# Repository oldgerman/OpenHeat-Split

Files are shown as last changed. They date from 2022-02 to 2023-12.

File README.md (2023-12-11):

# OpenHeat-Split

> 使用[朱雀固件](https://gitee.com/createskyblue/OpenT12)，PCB从[OpenHeat](https://github.com/peng-zhihui/OpenHeat)修改，主控引脚都不变，oled和编码器做成小板
>
> 该项目还包括热床外壳安装等~~一条龙服务~~
>
> <span style="color:rgb(255, 50, 50);">免责声明：不恰当的安装可能危及您的生命安全，请确保有一定的强电安全知识！</span>
>
> 本资料为压缩包版，不保证为最新版，最新版请访问[Github仓库](https://github.com/oldgerman/OpenHeat-Split)

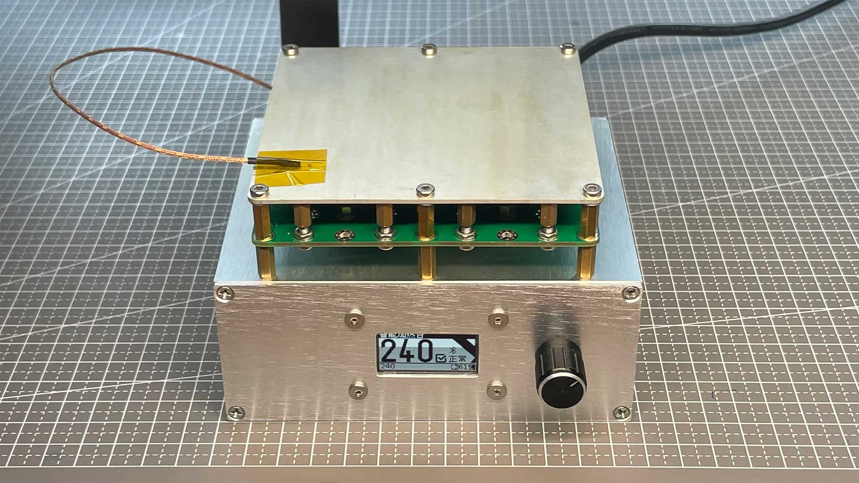
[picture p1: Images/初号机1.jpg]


## 控制板

- 使用0603封装、可靠性高的连接器
- oled和编码器做成单独的小板子，oled目前是1.3寸，可换2.42寸的（暂未画板，有能力的话可以自己做）
- 控制热床加热的MOS：使用便宜又大碗的TO-247封装的管子
- 推荐工作电压12~24V，电流小于18A

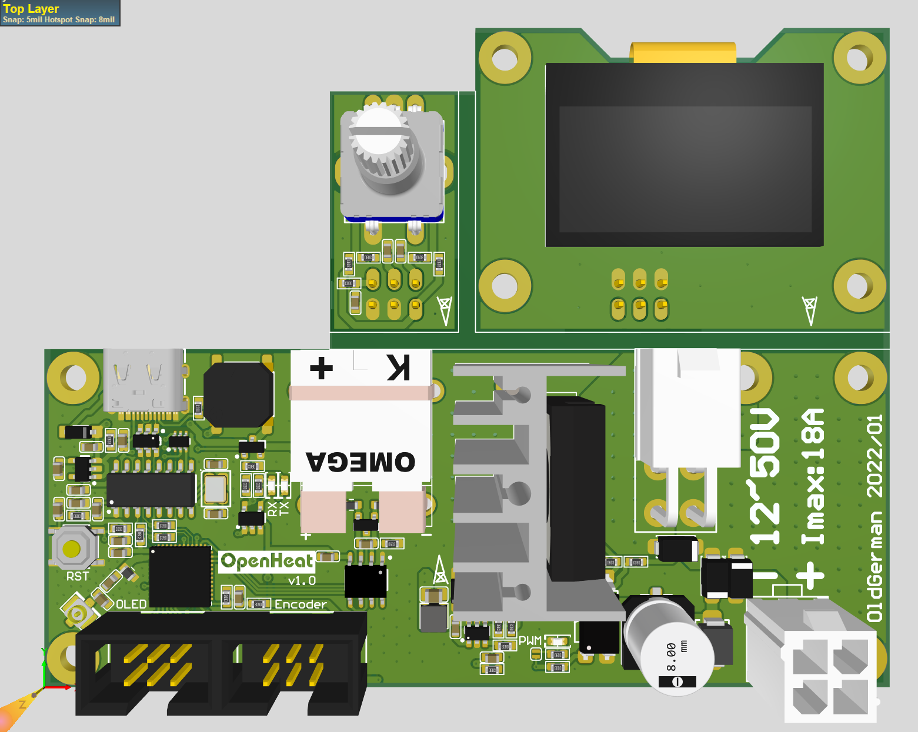
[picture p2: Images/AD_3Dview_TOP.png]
AD_3Dview
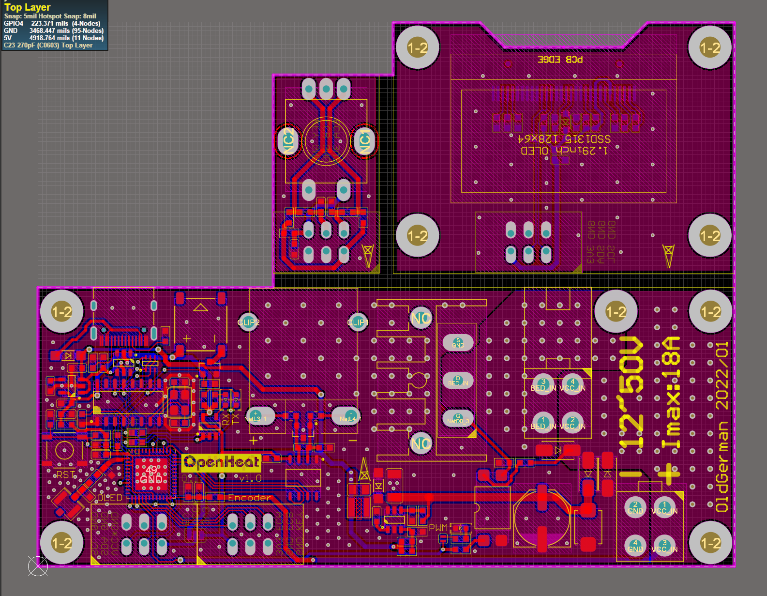
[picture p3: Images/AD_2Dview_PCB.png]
AD_2Dview
|  |  |
| --- | --- |

注：PCB为双面板，板厚1.6mm，需要分板，用壁纸刀沿着白线多划几下掰断，或者锯子伺候

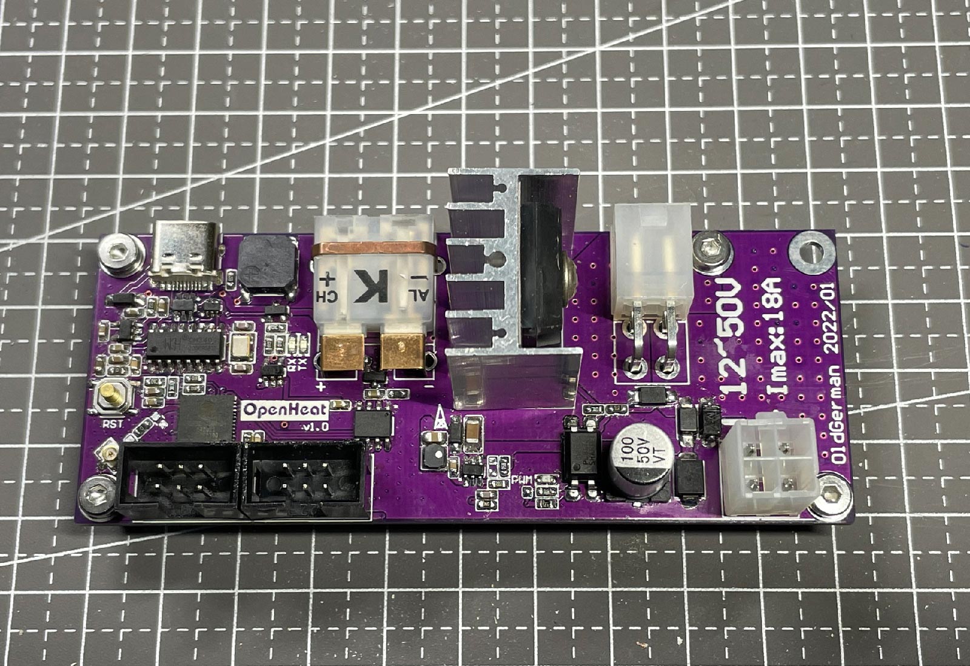
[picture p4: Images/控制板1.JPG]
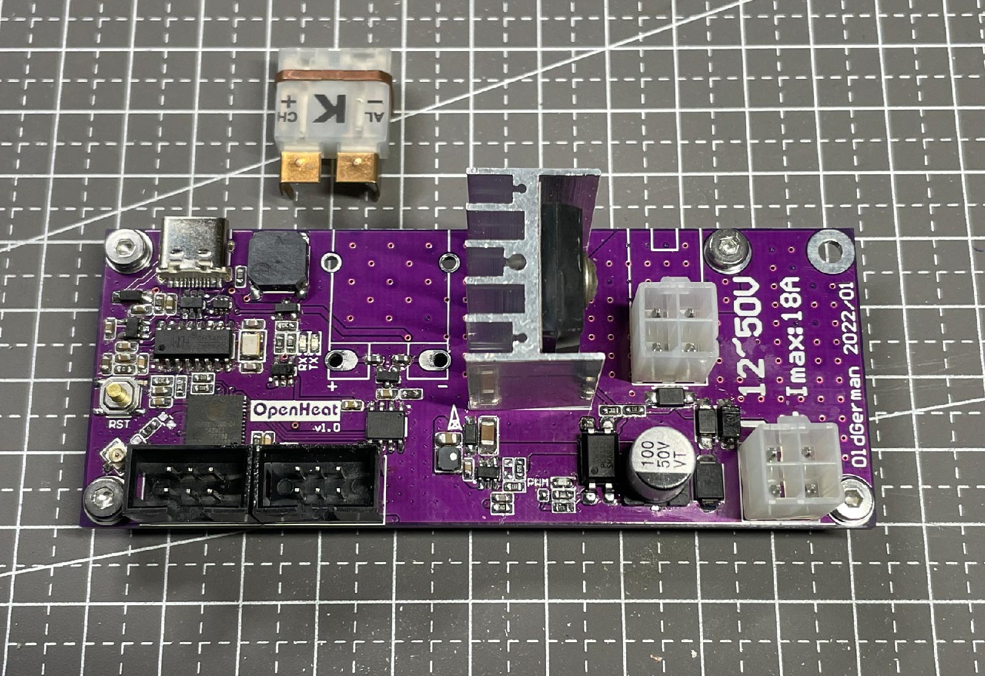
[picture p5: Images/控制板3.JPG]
|  |  |
| --- | --- |
| 接热床的4针端子使用90度的5569连接器 | 接热床的4针端子也可用垂直的5566连接器<br />若不安装K型热电偶连接器，可将热电偶丝直接焊接在焊盘上 |

## 热床

[GeekStart展硕](https://oshwhub.com/GeekStartzhan-shuo/GSH_Bed-lv-ji-ban-jia-re-ping-tai)设计的GSH Bed 12V150W版本，线宽28.347mil，实测12V只能加热到185度且此温度下功率约85W

我修改了该设计，将线加宽到43mil，两侧铜带开窗，使用类似探针方式的接触（免焊接），可通过配置“顶针”位置来兼容12V或24V，热床维持200度时功率约100W，维持230度功率约140W

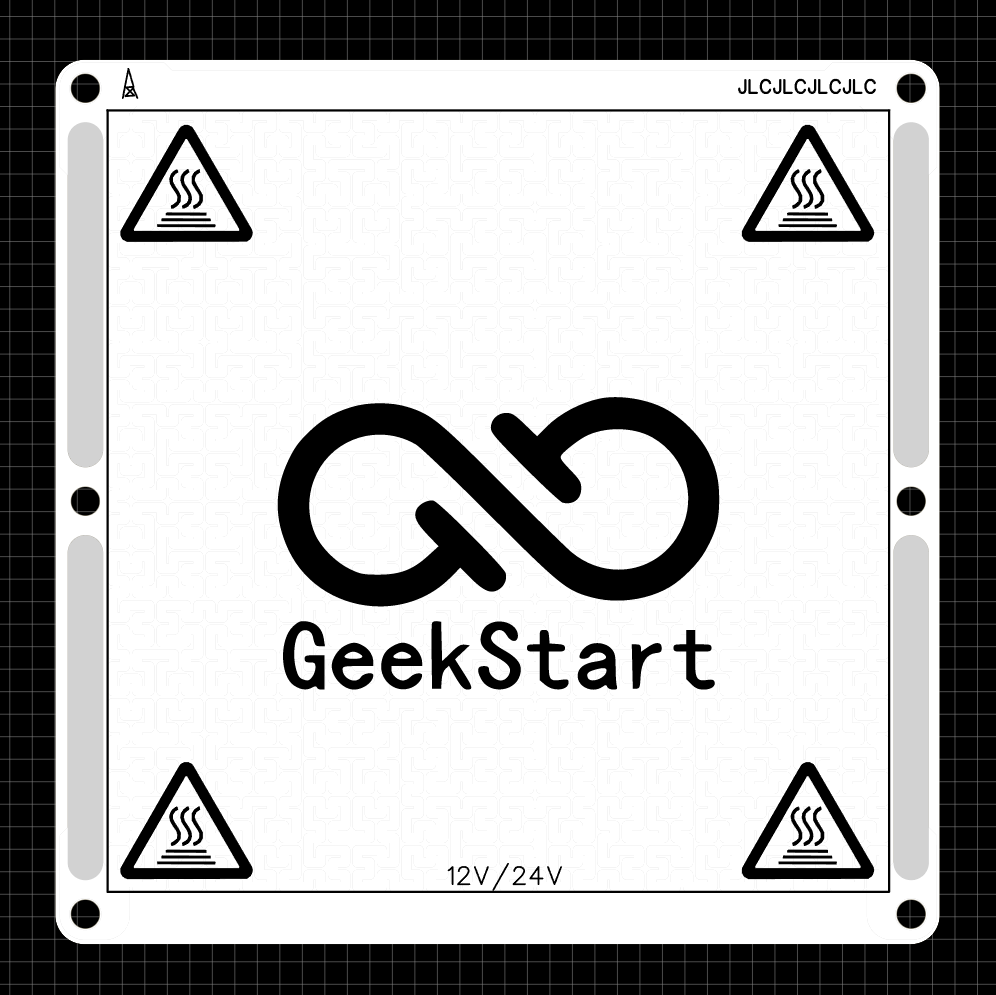
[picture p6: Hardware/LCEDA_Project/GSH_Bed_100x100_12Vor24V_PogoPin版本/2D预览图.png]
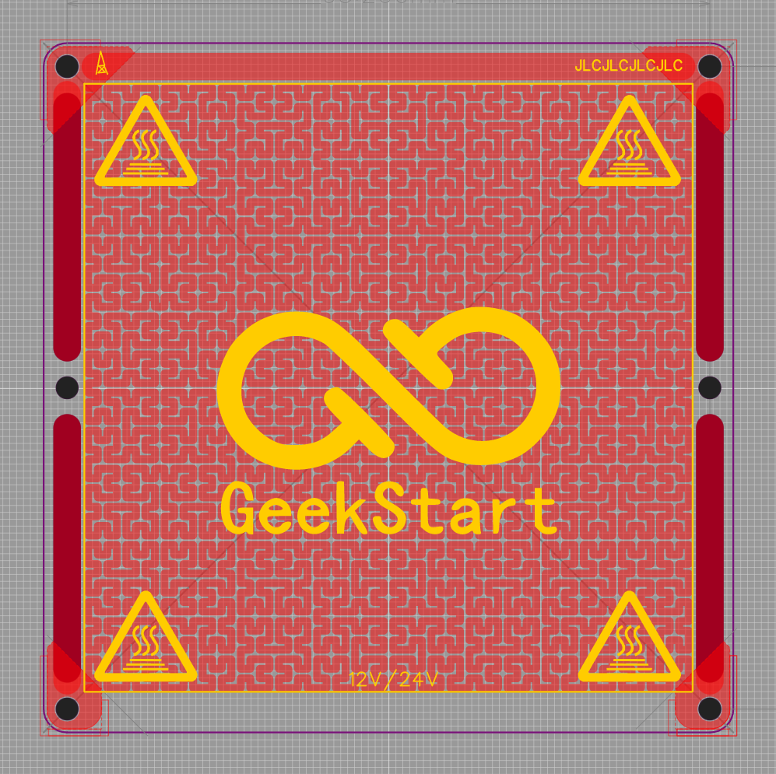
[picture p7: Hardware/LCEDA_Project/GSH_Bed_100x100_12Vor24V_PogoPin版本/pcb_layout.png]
|  |  |
| --- | --- |

### 升温测试

| 修改前：线宽28mil、Vin= 12.7V、T<sub>环境</sub> = 10℃，2段PID | 修改后：线宽43mil、Vin= 12.7V、T<sub>环境</sub> = 10℃，3段PID |
| --- | --- |
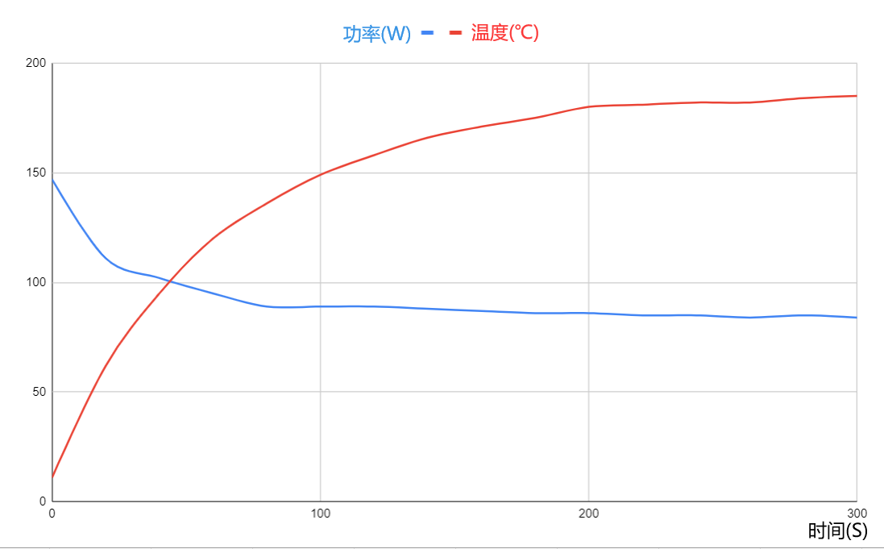
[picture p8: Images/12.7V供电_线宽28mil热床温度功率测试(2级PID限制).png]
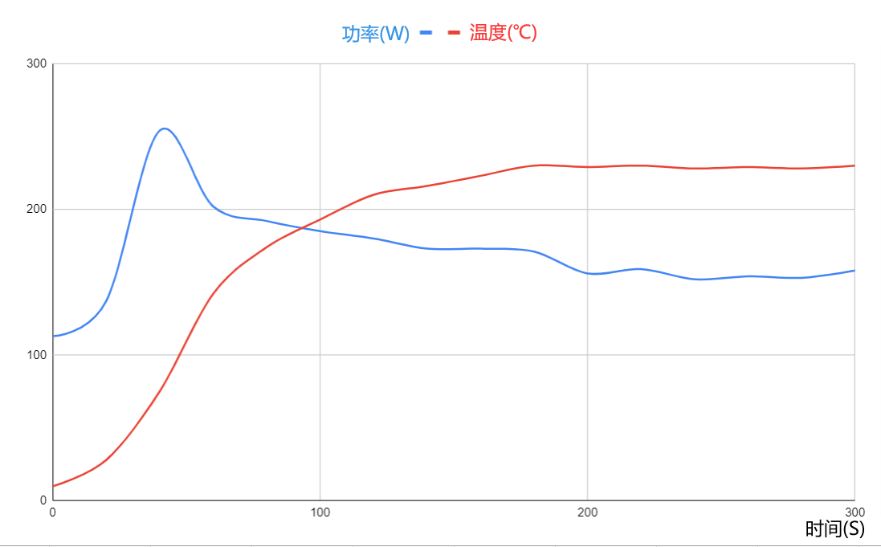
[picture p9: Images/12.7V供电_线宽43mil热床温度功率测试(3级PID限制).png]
|  |  |

## 顶针PCB

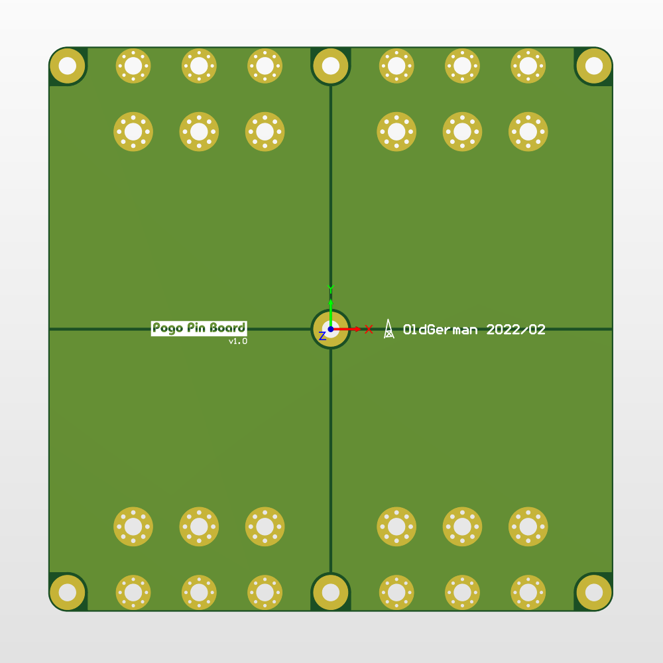
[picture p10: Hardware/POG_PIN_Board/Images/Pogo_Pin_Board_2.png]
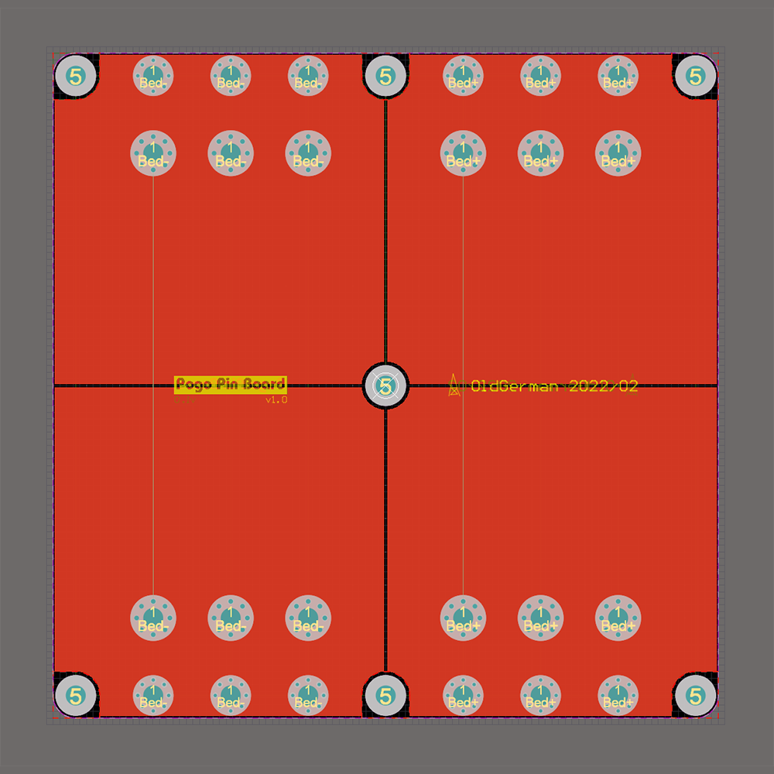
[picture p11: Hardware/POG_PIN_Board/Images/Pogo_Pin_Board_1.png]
|  |  |
| --- | --- |

### 为什么需要这块板？

1. 在铝基板和壳体之间隔热
2. 铝基板导热太强，供电线十分难焊接，且200度左右焊锡会软化
2. 我使用过[华容5A电流探针](https://item.taobao.com/item.htm?id=555813649830)与热床接触，探针铜镀金的，导热很快，当热床200度以上时探针内部的弹簧会失去弹性，使探针报废

### 顶针的位置

所以使用探针的计划翻车了，改用纯螺柱代替探针的接触方式，手搓铜柱顶住热床就行，这种接触方式姑且叫顶针吧，顶针用的螺丝螺柱的具体规格请见后文的 安装图：上壳体

可以通过配置顶针位置，使铝基板热床工作在12V或24V（许多3D打印机热床也有类似的设计），12V使用8枚顶针，24V使用4枚顶针

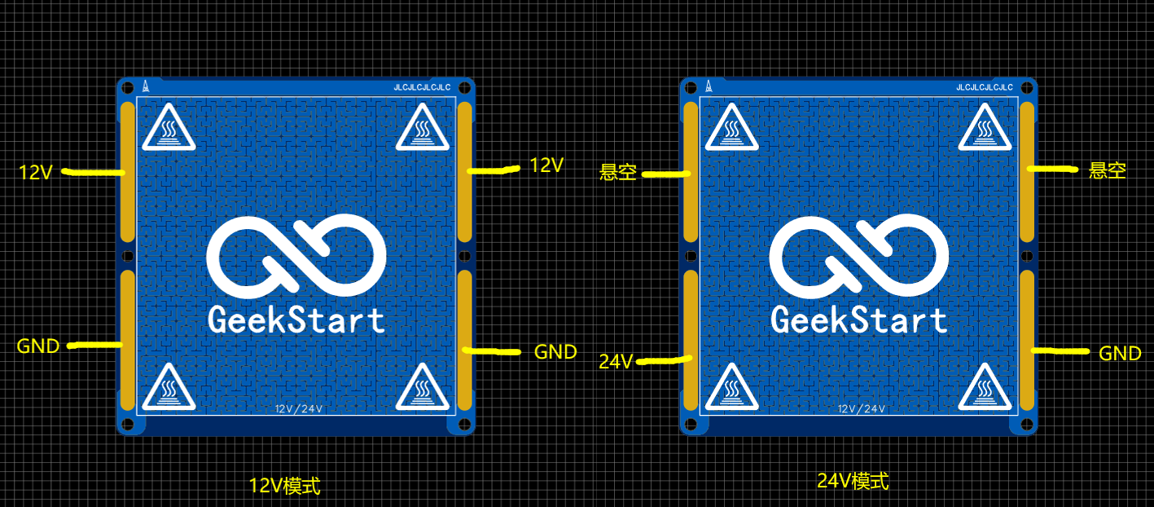
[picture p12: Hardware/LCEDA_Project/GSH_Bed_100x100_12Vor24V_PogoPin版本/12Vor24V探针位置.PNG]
12Vor24V探针位置


## 外壳

裸板并不意味着经久耐用，寻找合适的外壳是件头疼的事情

使用铝型材外壳，规格125×51×100mm，价格差不多15包邮，需要按开孔图开孔

### PCB尺寸

| | 尺寸（mm) | M3孔距（mm) |
| --- | --- | --- |
| 主控板 | 100×40 | 93.2×33.2 |
| 1.3寸OLED板 | 49×36 | 43×27 |
| 铝基板热床  | 100×100 | 93.2×93.2 |

为了做到安装不冲突，你可能需要修改本项目PCB源文件：最可能改动的是OLED小板的连接器位置，可见它并不居中，因为我根据目前用的<span style="color:rgb(0, 125, 255);">CLP0212</span>电源的尺寸做了修改，以防安装冲突

### 开关电源

电源可选型号如下，这类电源的尺寸大约是100×50mm，可以非常紧凑地安装在铝壳内

| | 开关电源 | 被动/主动散热功率(W) | 尺寸（mm) | 孔距（mm) | 加格(￥)@包邮 | 适配铝壳尺寸（mm) |
| --- | --- | --- | --- | --- | --- | --- |
| 厚度偏薄，利于前面板的模块安装 | 金升阳 LOF225 20bXX | 140/225 | 101.6×50.8×25.4  | 95.25×44.45 | 155 | 125×51×100 |
| 厚度偏厚，非常不利于前面板的模块安装 | 明纬 EPP-200-XX | 140/200 | 101.6×50.8×32 | 95.25×44.45 | 214 | 125×51×100 |
| 过气方案 | GE [CLP0212](https://library.industrialsolutions.abb.com/publibrary/checkout/CLP0212?TNR=Data%20Sheets%7CCLP0212%7CPDF) 12V | 100/200 | 101.6×50.8×37.14 | 93.2×42.4 | 45~196 | 125×51×100 |
| 又不是不能用 | [WX-DC2416](https://m.tb.cn/h.fQLvrV4?sm=300ae6) | 150/220 | 115×65×3.5 | 105.8×55.7  | 35 | 125×51×110 |

[参考：200W超小ITX电源 明纬EPP200-12性能测试](https://www.bilibili.com/read/cv14154464)

### 安装

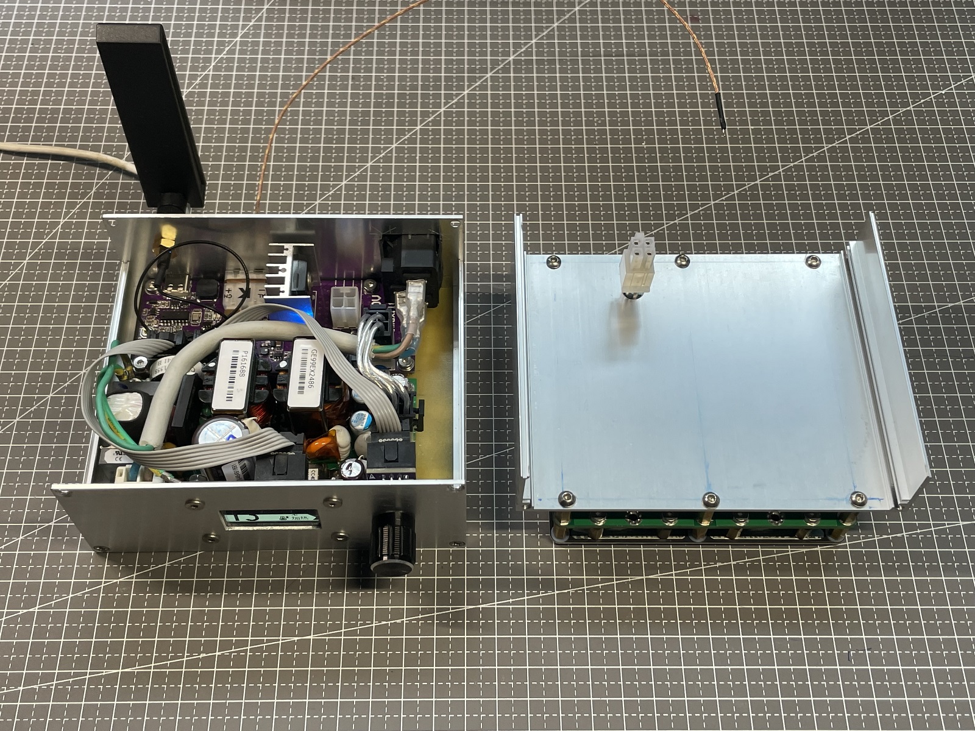
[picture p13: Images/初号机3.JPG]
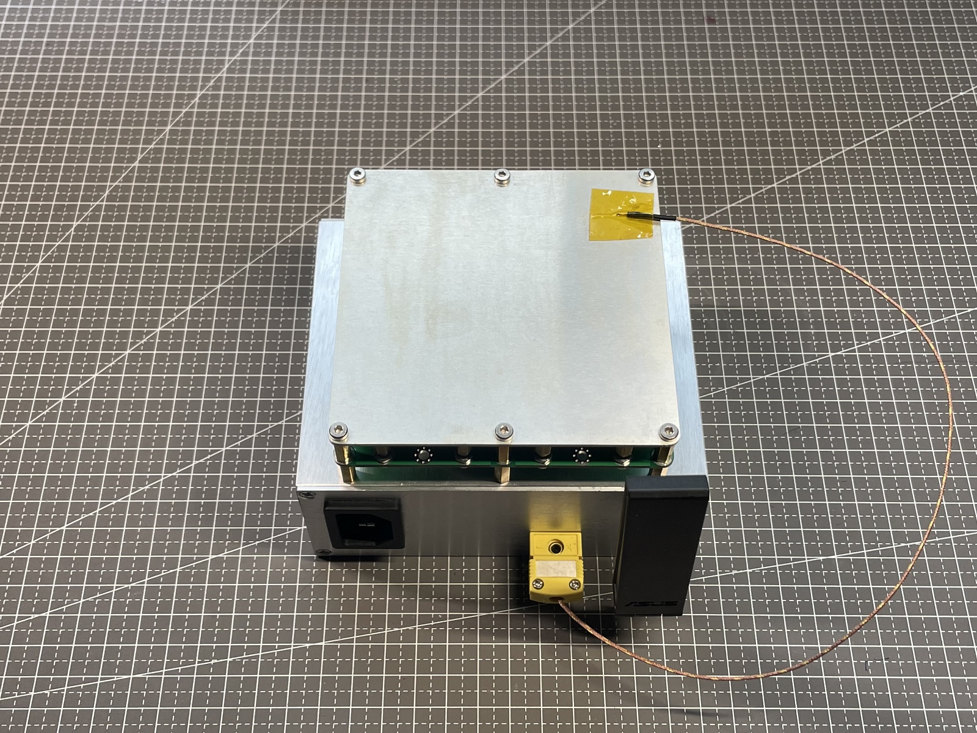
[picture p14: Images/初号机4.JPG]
| |  |  |
| --- | --- | --- |
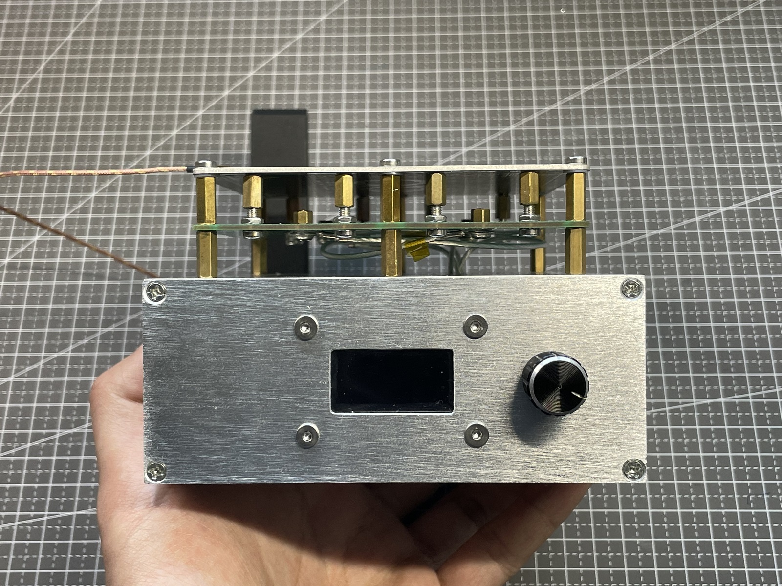
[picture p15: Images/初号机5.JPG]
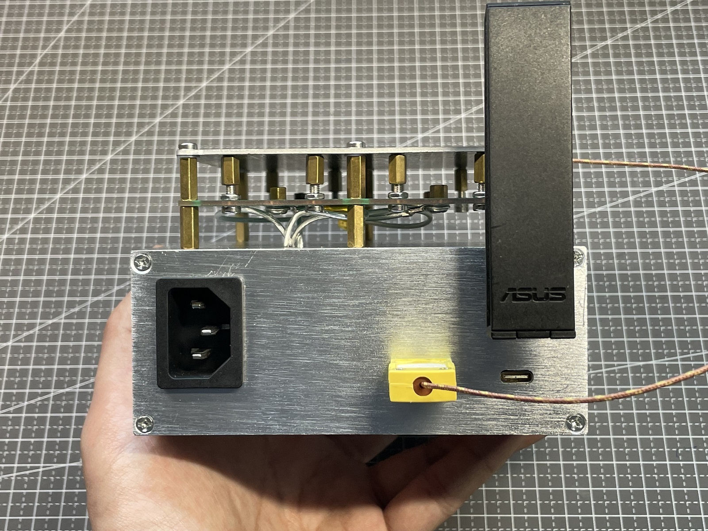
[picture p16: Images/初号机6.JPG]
| |  |  |
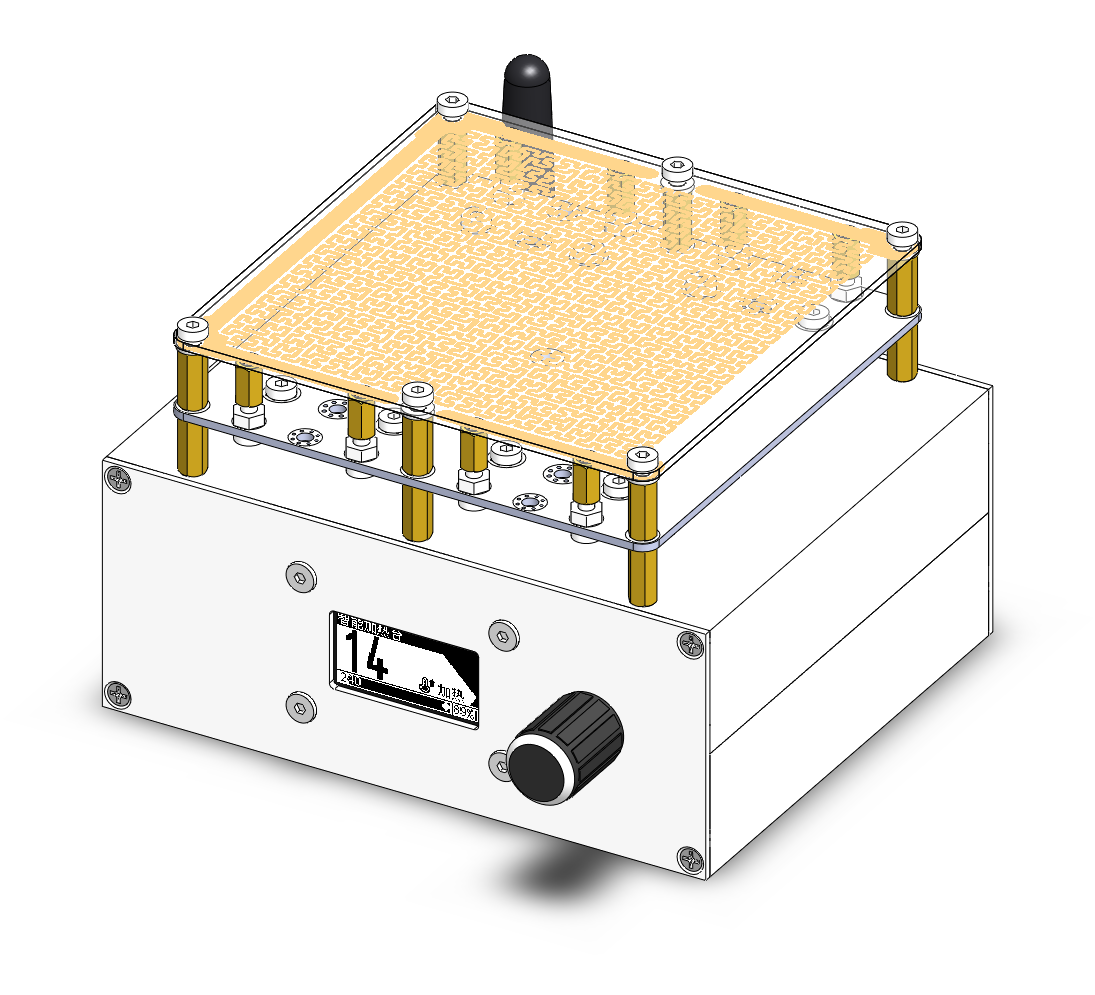
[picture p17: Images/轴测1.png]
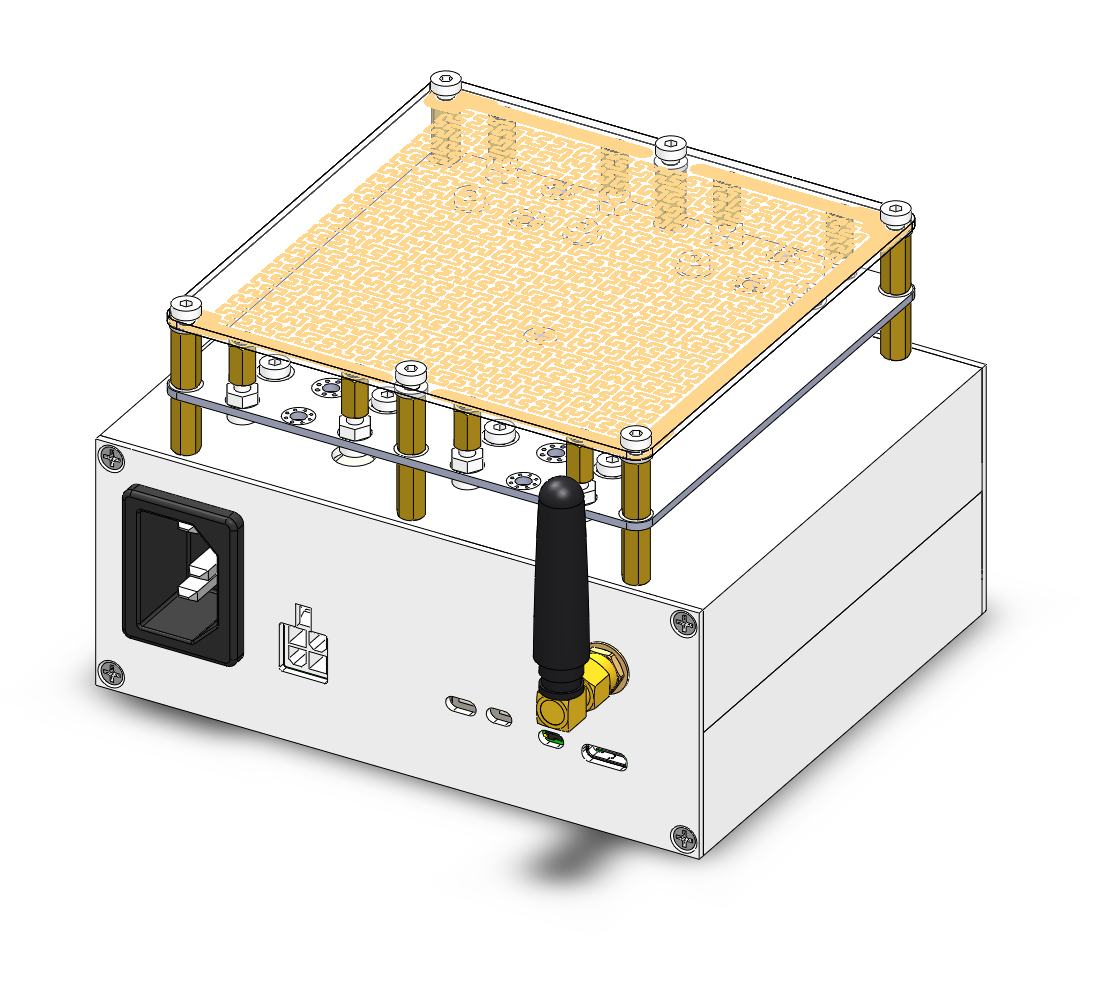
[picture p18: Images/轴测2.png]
| |  |  |
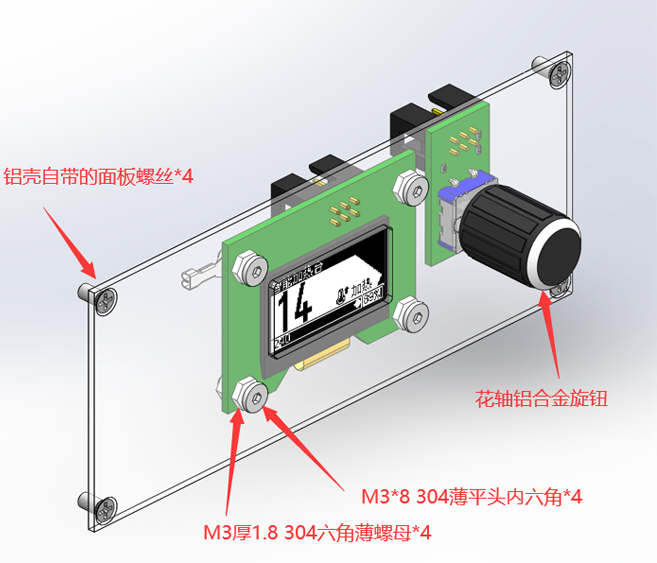
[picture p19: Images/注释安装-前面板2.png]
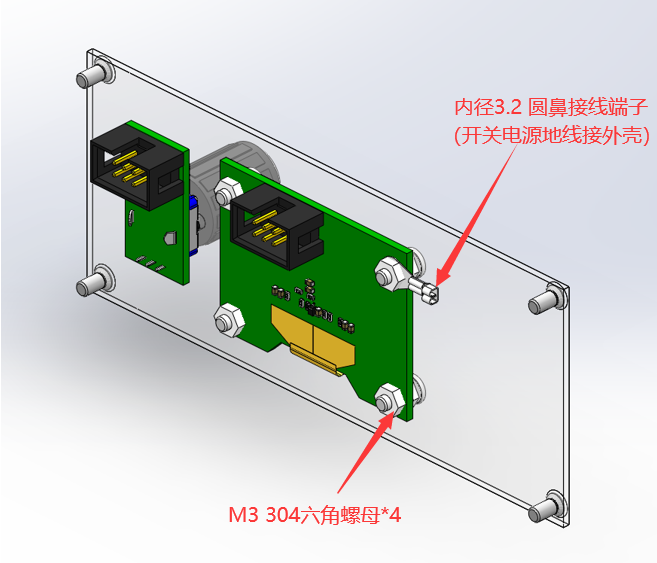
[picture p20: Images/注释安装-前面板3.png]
| 前面板 |  |  |
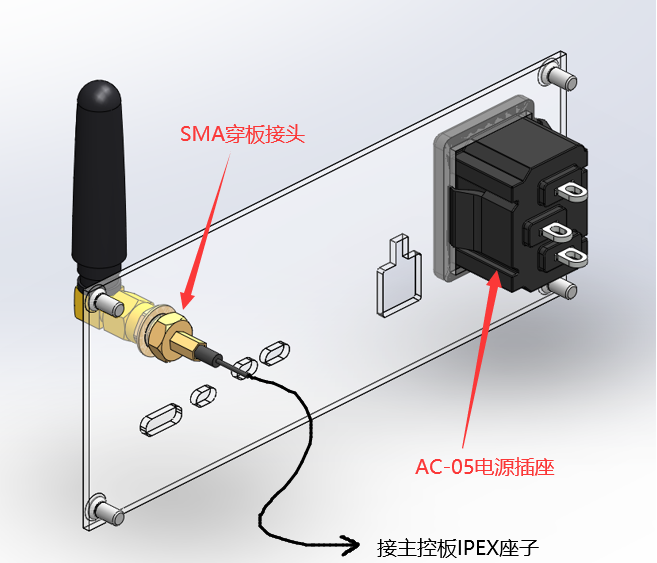
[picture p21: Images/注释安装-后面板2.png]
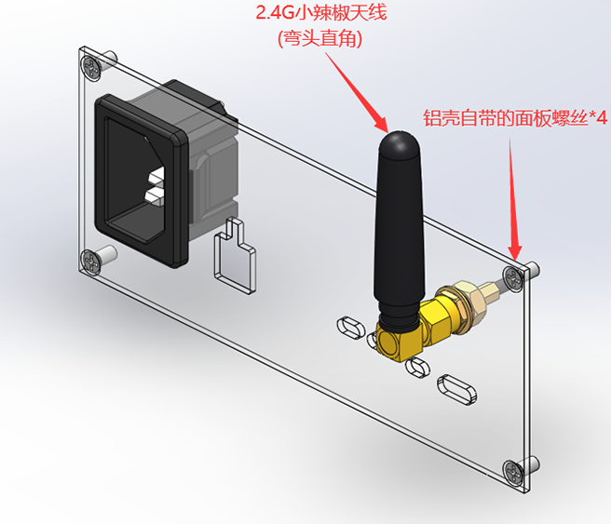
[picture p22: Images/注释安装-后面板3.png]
| 后面板 |  |  |
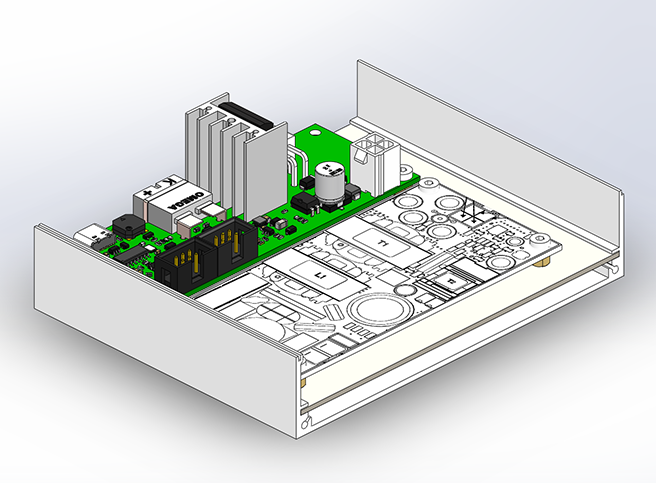
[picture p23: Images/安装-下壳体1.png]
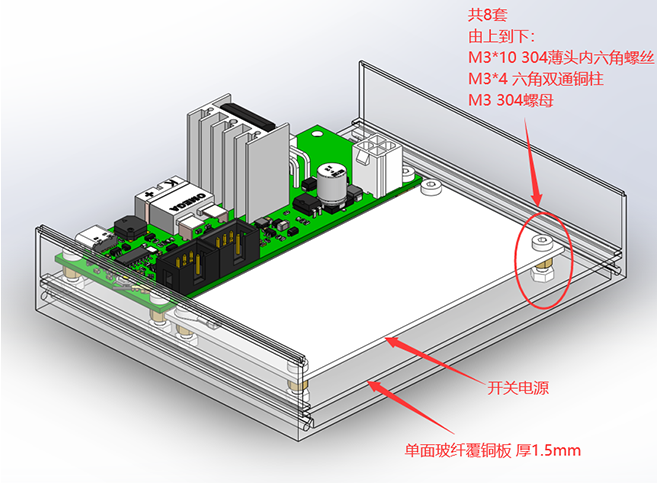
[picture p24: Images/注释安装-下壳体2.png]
| 下壳体 |  |  |
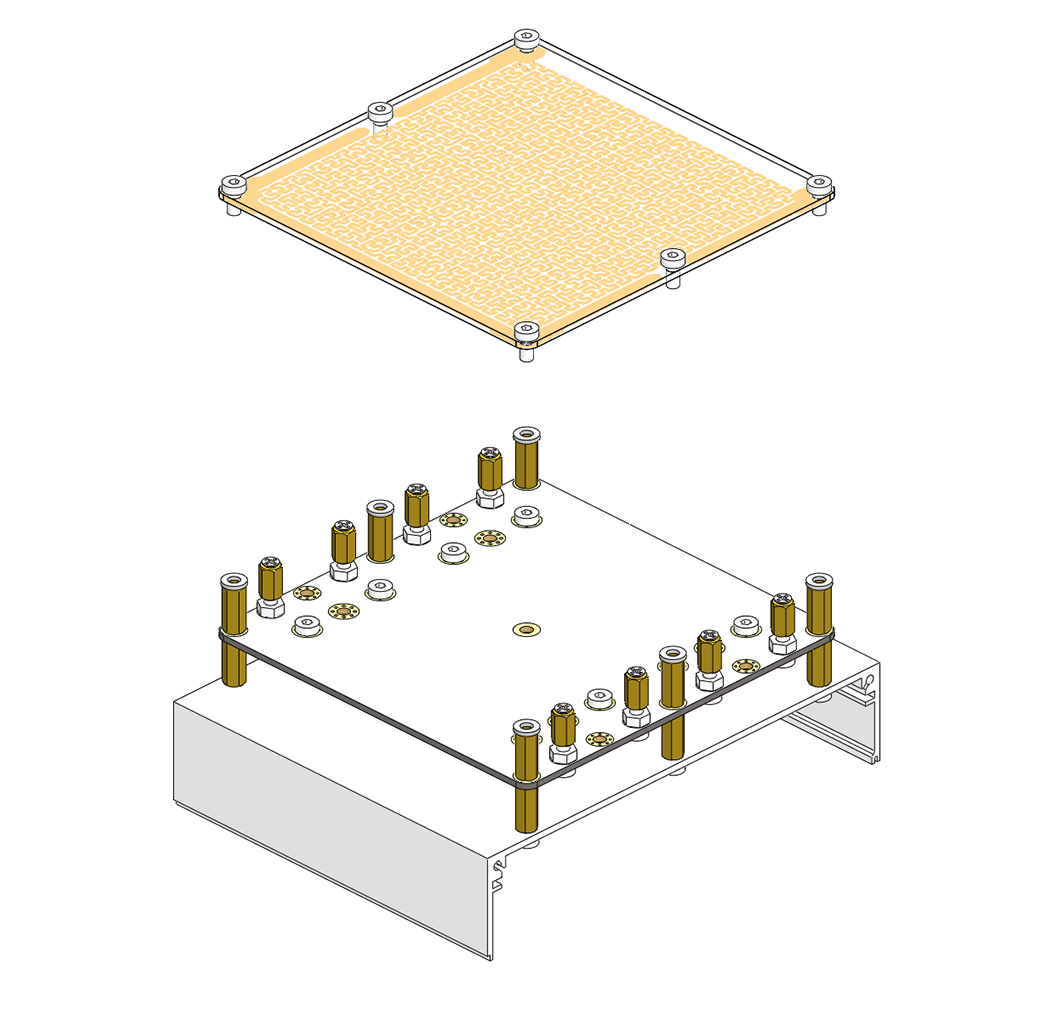
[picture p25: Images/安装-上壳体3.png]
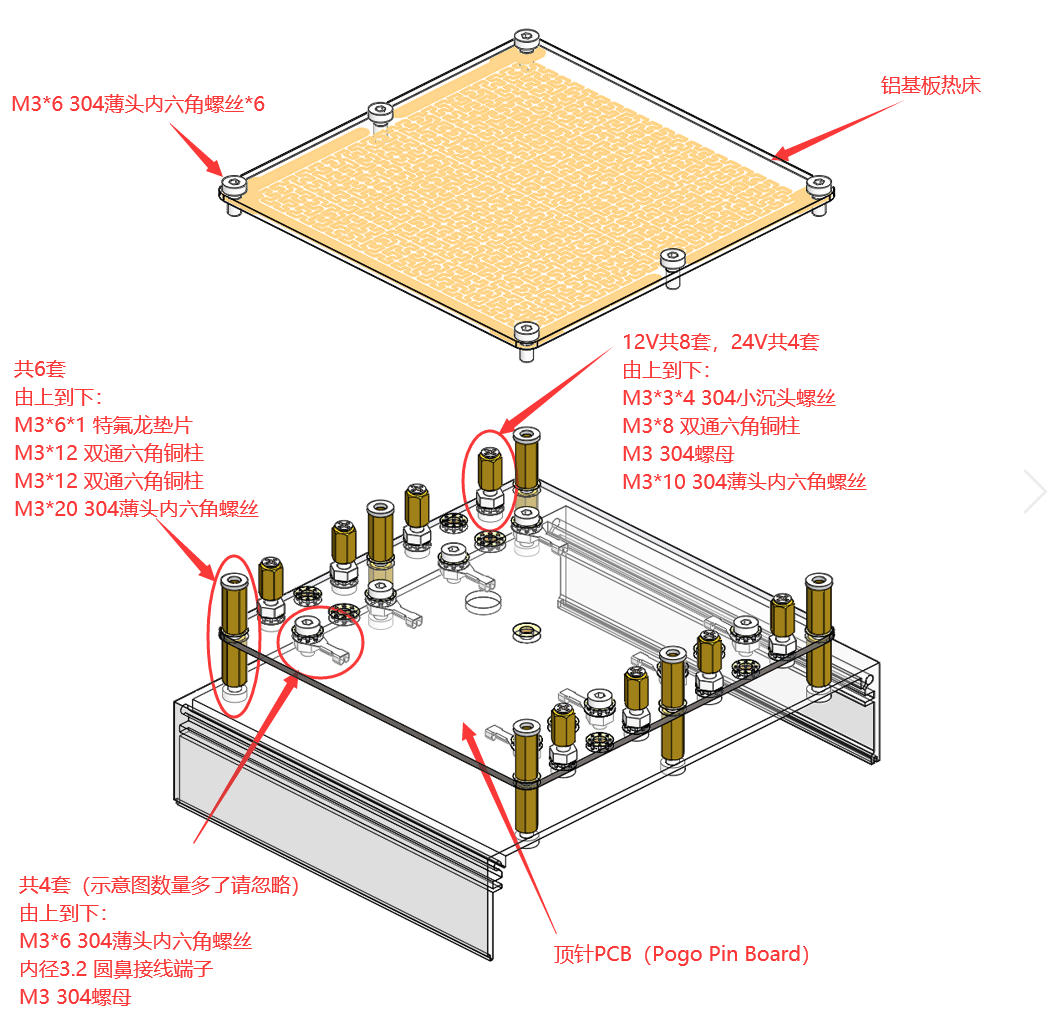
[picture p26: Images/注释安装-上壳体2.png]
| 上壳体 |  |  |

### 接地、绝缘

- 热床四个角的铜柱上<span style="color:rgb(255, 50, 50);">必须安装特氟龙垫片</span>（绝缘且耐240度高温），该垫片可以用规格3*6mm的特氟龙管手工切割制作
- AC-05电源插座<span style="color:rgb(255, 50, 50);">务必外套绝缘管</span>
- AC-05电源插座的地线、开关电源PCB的接地专用的固定孔、oled显示屏螺丝处的外壳接地点，<span style="color:rgb(255, 50, 50);">三个接地点务必可靠连接</span>
- 开关电源是裸板，PFC的MOS电压可达380V以上，需<span style="color:rgb(255, 50, 50);">注意开关电源板边沿与铝制外壳的距离</span>

### 铝壳开孔

开孔图纸提供了CAD文件，前后面板若自己开孔太麻烦，可以做成铝基板代替

控制板接热床可选两种连接器，对应不同的引出线方式：

- 若使用5569连接器，热床的电线从后面板引出
- 若使用5566连接器，热床的电线从上壳体圆洞引出

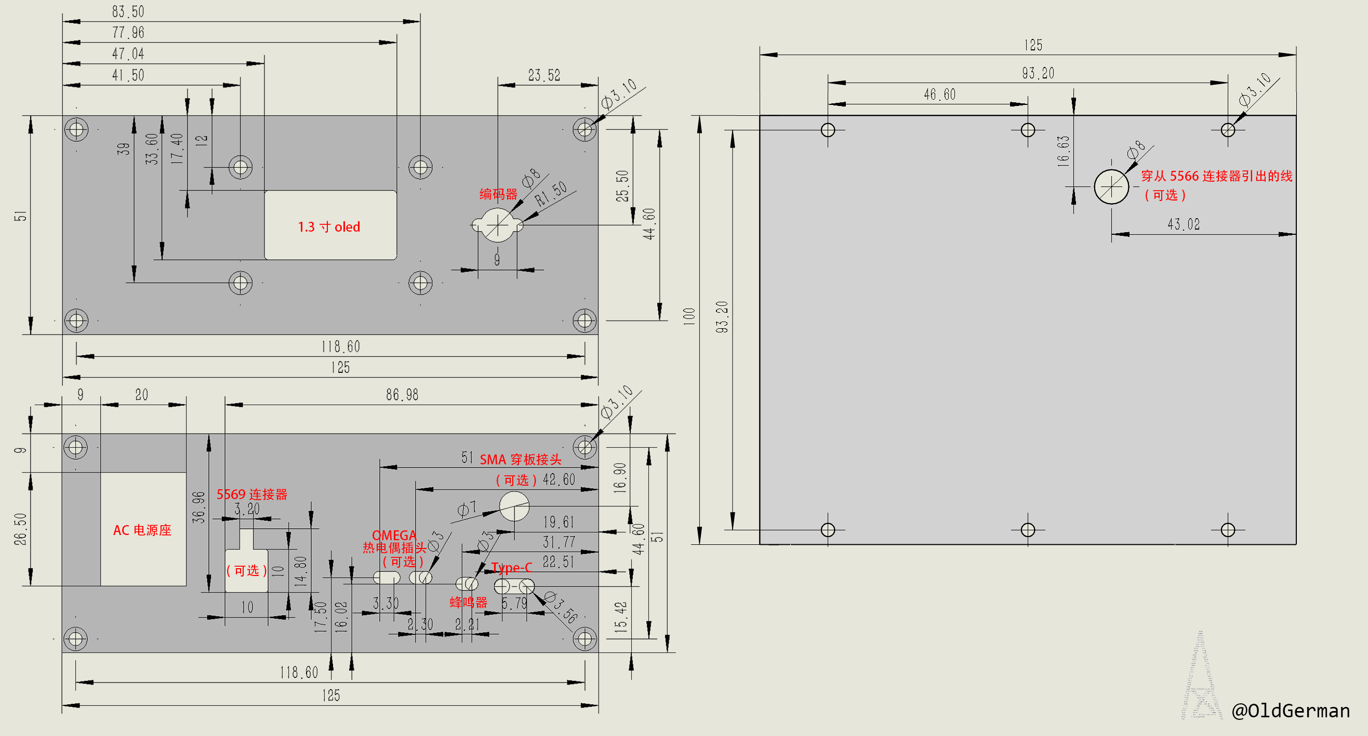
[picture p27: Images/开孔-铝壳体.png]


### 抽拉板开孔

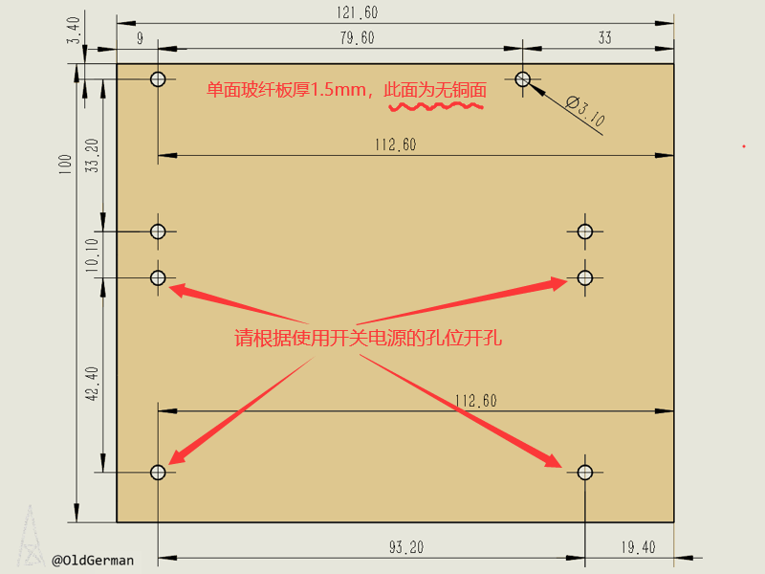
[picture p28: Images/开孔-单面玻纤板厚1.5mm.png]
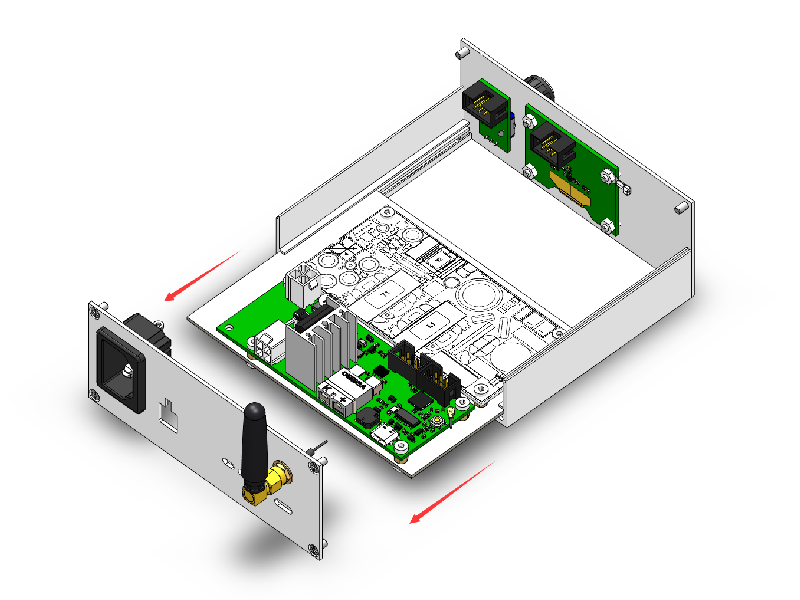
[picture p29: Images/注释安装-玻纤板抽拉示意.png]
|  |  |
| --- | --- |

## 程序

### 烧录前的准备工作

感谢[B站谢培宇x 适配好了MAX6675](https://b23.tv/DqndTQK)，[程序](https://pan.baidu.com/s/1FN_KfvtdgoIdXALv11UErQ) 提取码: 7fx5，VsCode环境搭建&程序烧录也推荐看他的视频教程

### 热床功率过大导致开关电源限流保护

朱雀固件原程序有两组可配置的PID，一组负责爬升期，一组负责接近期

虽说推荐使用的200W以上的开关电源，但探针版GSH_Bed热床在0温升时，功率约288W，因此常温时若直接通电，程序直接按爬升区计算，使开关电源全功率加热，会触发开关电源短路保护

减小热床线宽可以降低电流，但测试43mil线宽热床，维持230度时PID输出的占空比在84%~100%之间波动，减小热床线宽可能会无法维持到230度

#### 方法1

增加一组可配置的预备期PID和预备温度，用于预备升温，等温度升高到热床内阻增大到 开关电源全功率负载不会触发短路保护时，再切换为爬升区PID，<span style="color:rgb(255, 50, 50);">修改后的程序在 Firmware 文件夹内</span>，预备期PID的值需要需要根据电源测试

#### 方法2

尝试修改温控曲线，限制最大输出功率，但目前曲线部分代码有显示问题，等本id有空试试

## Tips

1. 热床工作温度？
   
   <span style="color:rgb(255, 50, 50);">请特别注意</span>铜箔与铝板之间的绝缘层在<span style="color:rgb(255, 50, 50);">260度</span>以上会失效，建议<span style="color:rgb(255, 50, 50);">工作温度不超过260度</span>
   
   > 当前仓库源码最高温为260度，可通过 `OpenT12.h` 的`TipMaxTemp`进行修改：
   >
   > ```c
   > #define TipMaxTemp 260
   > ```
   
2. 热床阻焊层变黄？

   铝基板热床是消耗品，测试在环境温度10℃时，温度在180度时白油阻焊层几乎不会变黄，200度左右开始泛黄，建议PCB打样时选择无阻焊或黑色阻焊

3. 热床表面残留的的助焊剂污渍洗板水洗不掉？

   用800目砂纸稍加打磨
   
3. 加热有时oled花屏？（已解决）

   此情况热床温度在100度以下时容易出现，来源于开关电源的电磁干扰，目前暂未找到比较好的解决方法，当热床温度到150度以上时这种现象消失
   
   > ## 2023/12/11
   >
   > 解决方法：修改`TipControl.cpp`的`PWM_Freq`：
   >
   > ```c
   > double PWM_Freq = 50000;    // uint8_t类型写错了，改为double类型
   >                             // 将频率从默认的2000改为50000，开关电源模块电感没有吱吱响声了
   >                             // 备注：PC817 光耦带宽 81KHz
   > ```
   >
   > 修改后，实测能达到的最高温度没多大影响，改前最高245度，改后242度，关键是开关电源电感不啸叫了，这点非常Nice

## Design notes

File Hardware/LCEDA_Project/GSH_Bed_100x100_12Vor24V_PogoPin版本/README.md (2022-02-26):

## 热床

下单选择铝基板（单层）
PCB尺寸99.82mm x 99.82mm
m3固定孔，孔距93.2x93.2mm
附立创EDA工程文件

原作者：
[GSH_Bed 铝基板加热平台](https://oshwhub.com/GeekStartzhan-shuo/GSH_Bed-lv-ji-ban-jia-re-ping-tai)

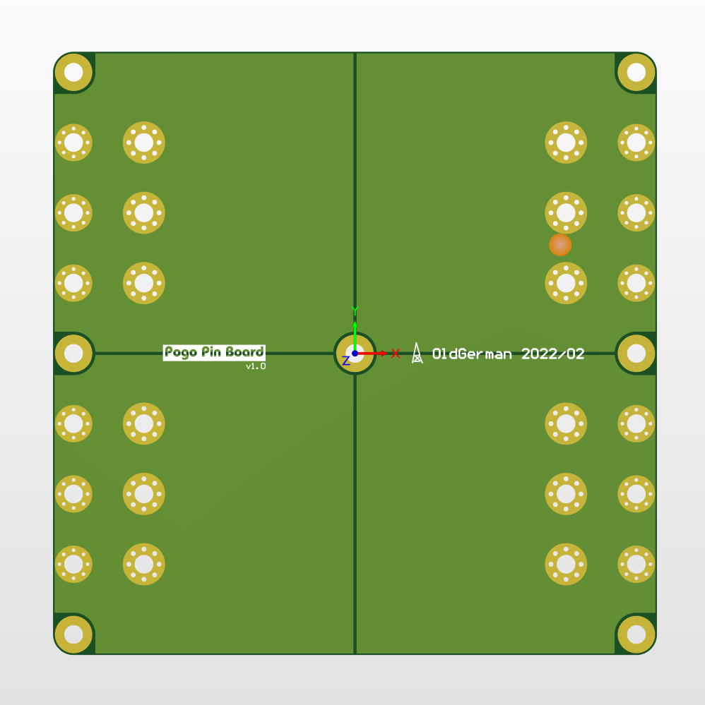
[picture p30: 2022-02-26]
Hardware/POG_PIN_Board/Images/Pogo_Pin_Board_3.png

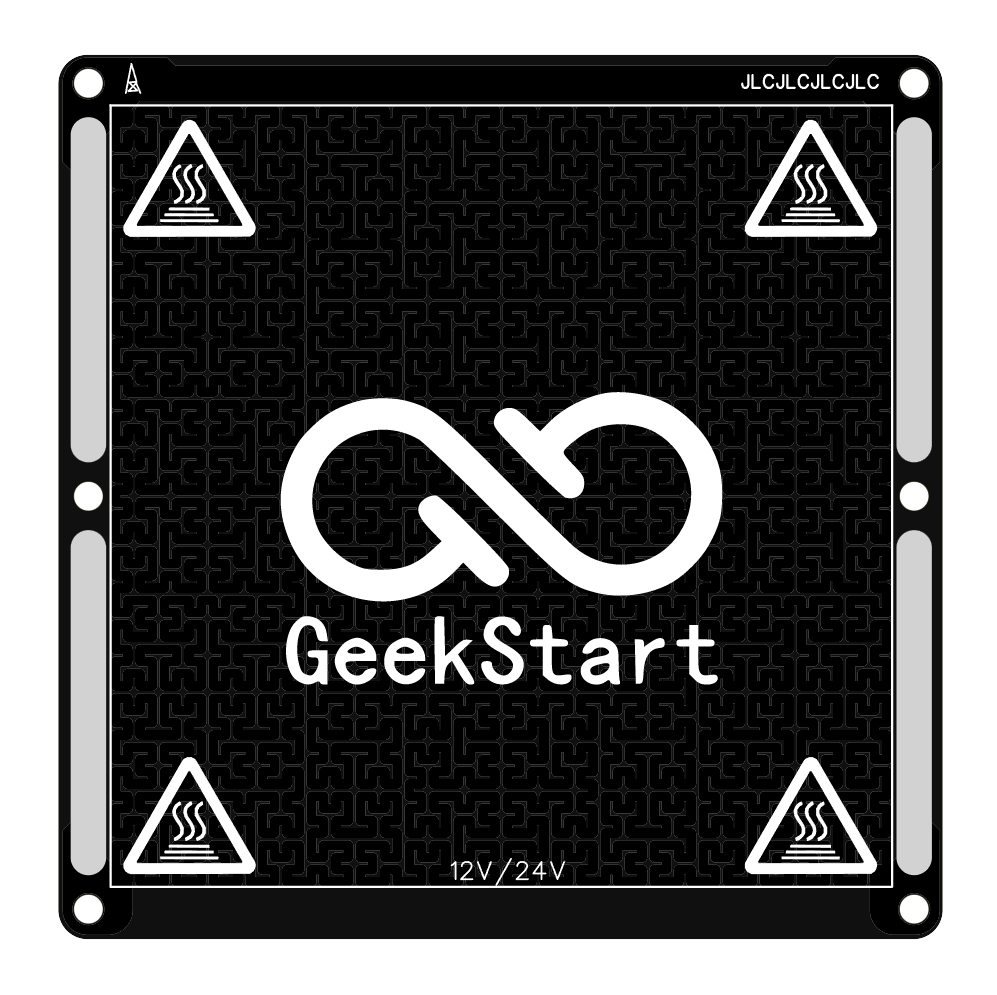
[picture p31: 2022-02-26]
Hardware/LCEDA_Project/GSH_Bed_100x100_12Vor24V_PogoPin版本/2D预览图-2.png

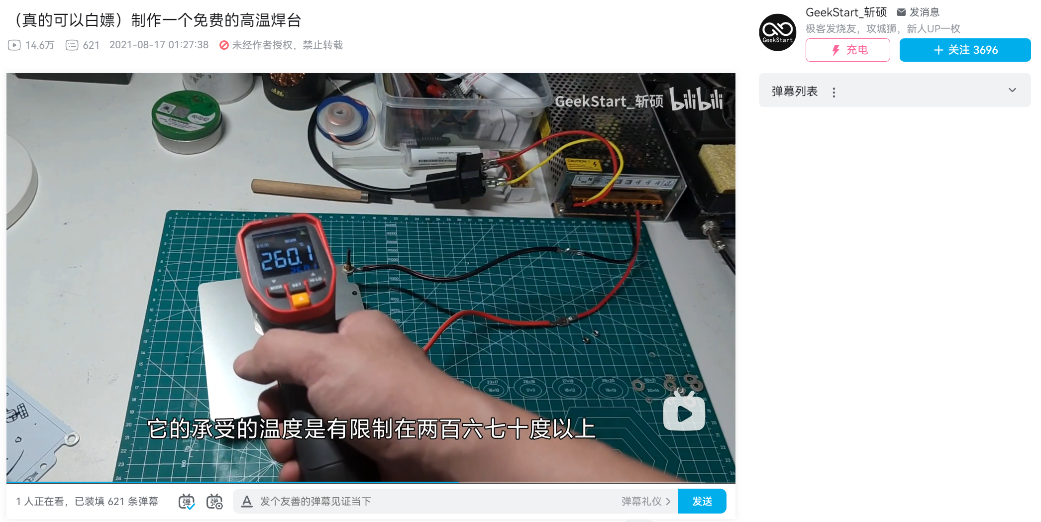
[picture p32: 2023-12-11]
Images/PCB绝缘层承受的温度限制.png

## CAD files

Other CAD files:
Hardware/开孔尺寸图纸CAD/125X51-铝壳-前面板.DWG
Hardware/开孔尺寸图纸CAD/125X51-铝壳-壳体.DWG
Hardware/开孔尺寸图纸CAD/125X51-铝壳-后面板.DWG
Hardware/开孔尺寸图纸CAD/单面玻纤板121x100x1.DWG

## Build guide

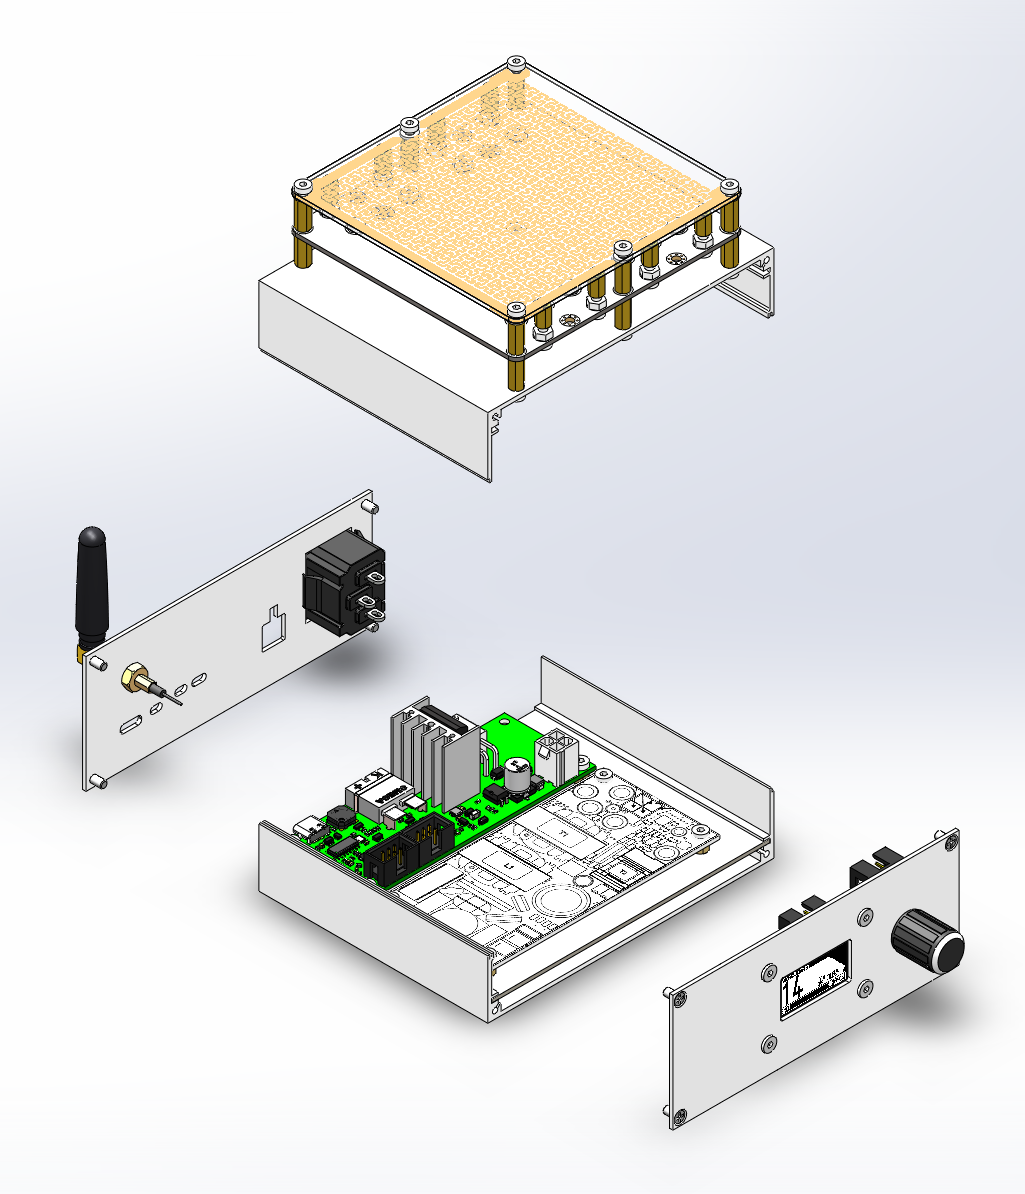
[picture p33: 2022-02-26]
Images/组装1.png

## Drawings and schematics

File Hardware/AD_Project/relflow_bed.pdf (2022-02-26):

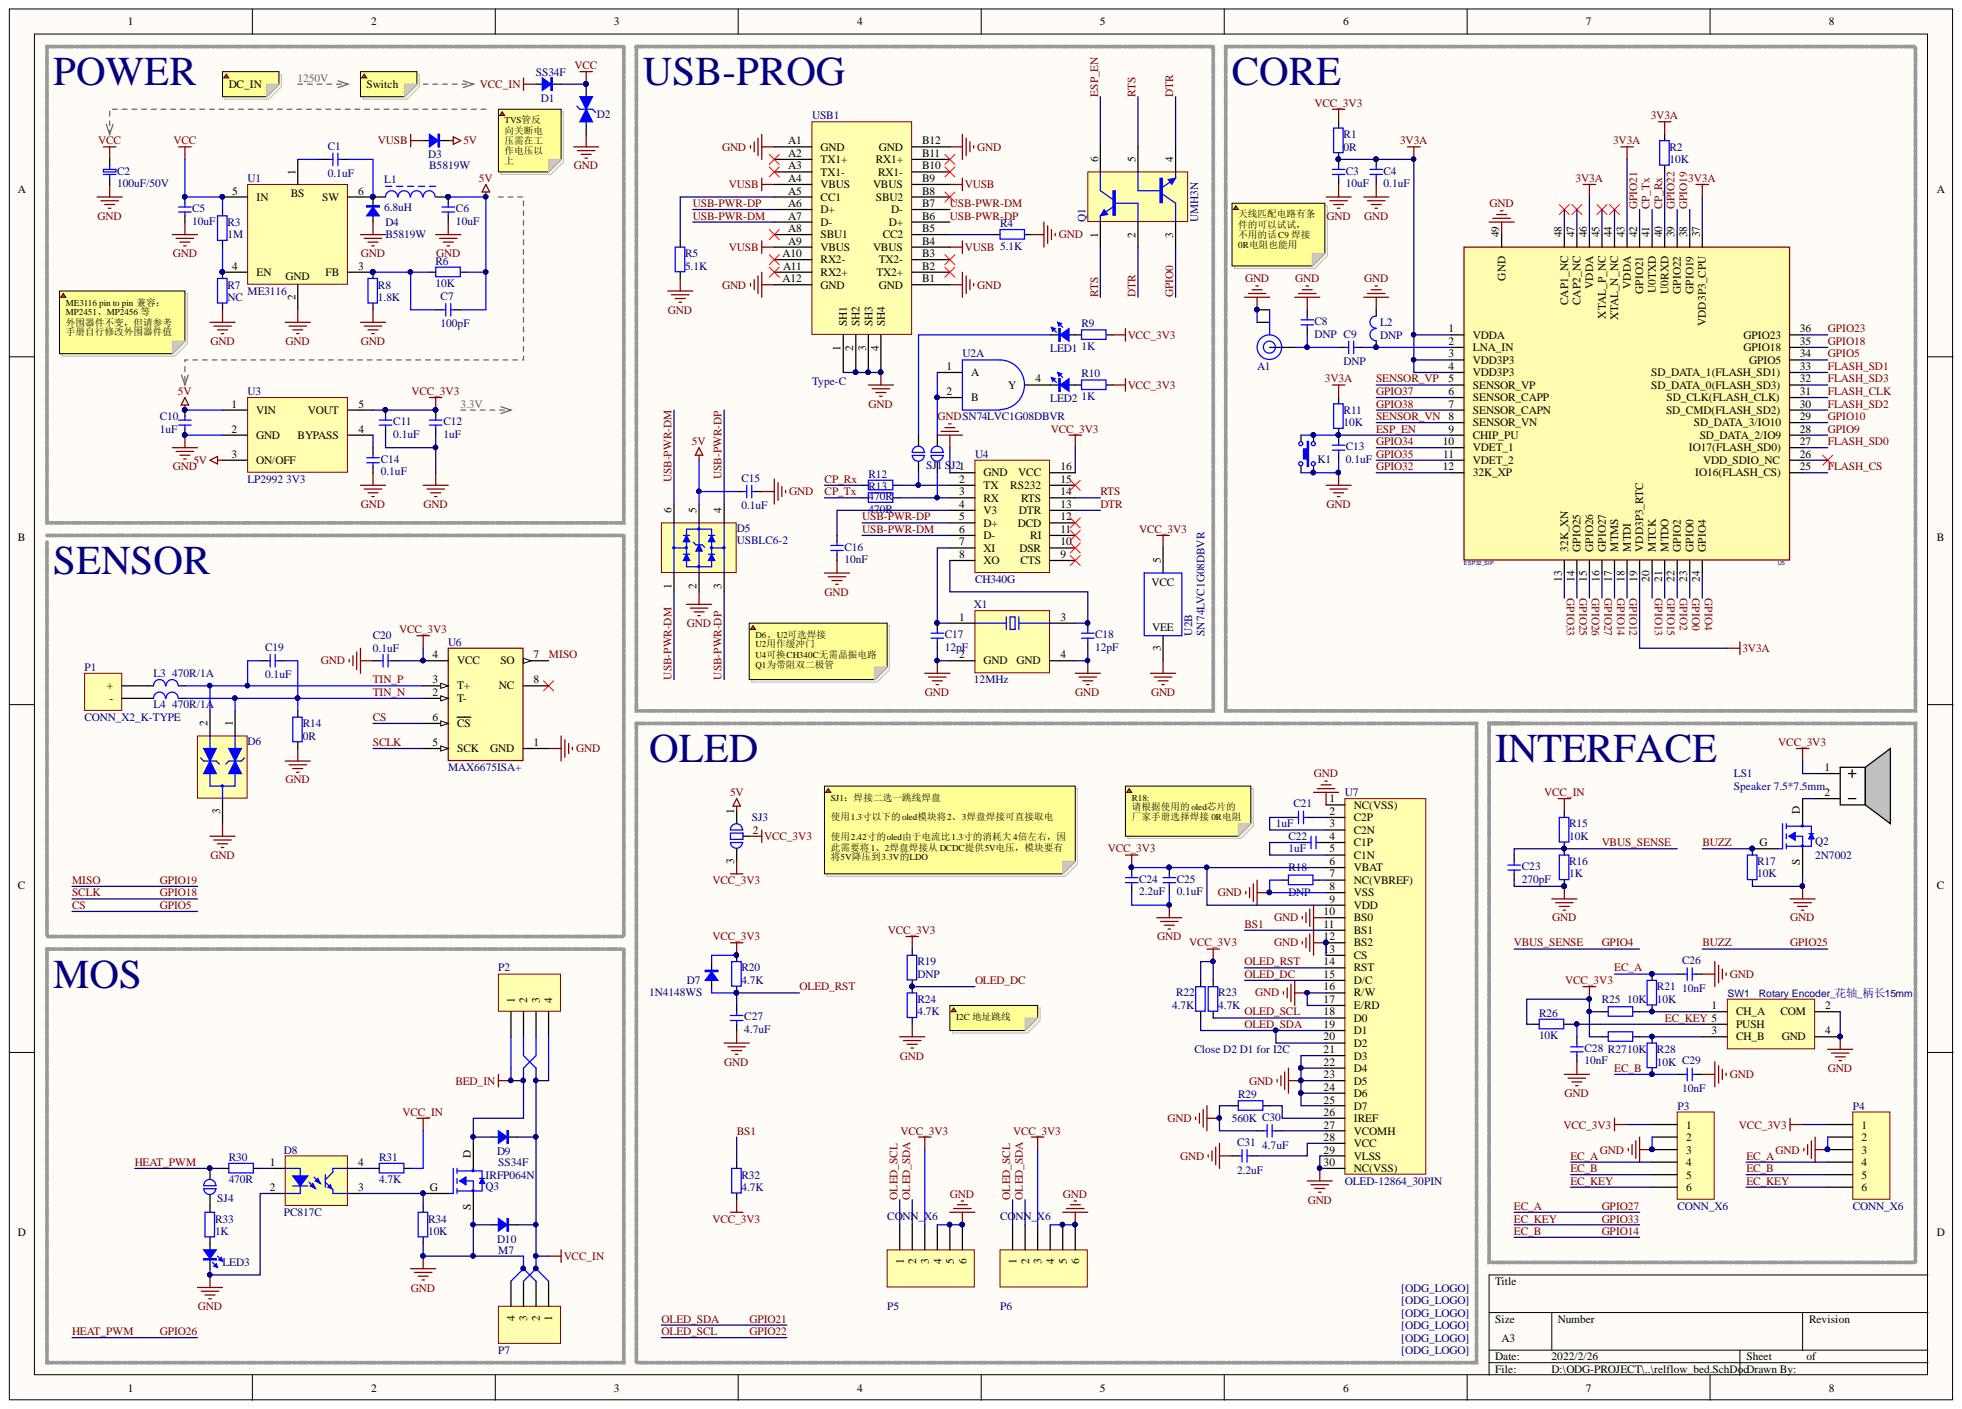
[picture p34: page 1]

USB-PWR-DP

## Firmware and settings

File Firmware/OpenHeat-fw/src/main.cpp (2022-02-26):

#include <Arduino.h>

#include "soc/soc.h"
#include "soc/rtc_cntl_reg.h"
#include "OpenT12.h"


BluetoothSerial SerialBT;
#if !defined(CONFIG_BT_ENABLED) || !defined(CONFIG_BLUEDROID_ENABLED)
#error Bluetooth is not enabled! Please run `make menuconfig` to and enable it
#endif

OneButton RButton(BUTTON_PIN, true);
U8G2_SSD1306_128X64_NONAME_F_HW_I2C Disp(U8G2_R0, /* reset=*/ U8X8_PIN_NONE, /* clock=*/ 22, /* data=*/21);
PID MyPID(&TipTemperature, &PID_Output, ptr_PID_Setpoint, aggKp, aggKi, aggKd, DIRECT);
/////////////////////////////////////////////////////////////////

char* TipName = "文件系统错误：请上报";

float ReadyTemp = 50;      //预备温度，防止上电瞬间电流过大导致开关电源短路保护          (°C)
double offset_ReadyTemp = 0; //预备温度偏移
float BootTemp = 100;      //开机温度          (°C)
float SleepTemp = 100;     //休眠温度          (°C)
float BoostTemp = 50;      //爆发模式升温幅度   (°C)

float ShutdownTime = 0;      //关机提醒              (分)
float SleepTime = 10;      //休眠触发时间          (分)
float ScreenProtectorTime = 60;     //屏保在休眠后的触发时间(秒)
float BoostTime = 60;     //爆发模式持续时间      (秒)


bool SYS_Ready = false;
//烙铁头事件
bool TipInstallEvent = true;
bool TipCallSleepEvent = false;
//到温提示音播放完成
bool TempToneFlag = false;
//休眠后屏保延迟显示标志
bool SleepScreenProtectFlag = false;
//温控系统状态
bool ERROREvent = false;
bool ShutdownEvent = false;
bool SleepEvent = false;
bool BoostEvent = false;
bool UnderVoltageEvent = false;
//PWM控制状态
bool PWM_WORKY = false;

uint8_t PIDMode = true;
uint8_t Use_KFP = true;
uint8_t PanelSettings = PANELSET_Detailed;
uint8_t ScreenFlip = false;
uint8_t SmoothAnimation_Flag = true;
float ScreenBrightness = 128;
uint8_t OptionStripFixedLength_Flag = false;

uint8_t Volume = true;
uint8_t RotaryDirection = false;
uint8_t HandleTrigger = HANDLETRIGGER_VibrationSwitch;

double SYS_Voltage = 3.3;
float UndervoltageAlert = 3;
char BootPasswd[20] = {0};
uint8_t Language = LANG_Chinese;
uint8_t MenuListMode = false;

float ADC_PID_Cycle = 100;

//面板状态条
uint8_t TempCTRL_Status = TEMP_STATUS_OFF;
uint8_t* C_table[] = {c1, c2, c3, Lightning, c5, c6, c7};
char* TempCTRL_Status_Mes[] = {
    "错误",
    "停机",
    "休眠",
    "提温",
    "正常",
    "加热",
    "维持",
};

//系统信息
uint64_t ChipMAC;
char ChipMAC_S[19] = {0};
char CompileTime[20];

int thermoDO = 19;
int thermoCS = 5;
int thermoCLK = 18;
MAX6675 *thermocouple;
MAX6675 thermocouple1(thermoCLK, thermoCS, thermoDO);


/////////////////////////////////////////////////////////////////

//先初始化硬件->显示LOGO->初始化软件
void setup()
{
    WRITE_PERI_REG(RTC_CNTL_BROWN_OUT_REG, 0); //disable brownout detector
    //关闭中断
    noInterrupts();

    ////////////////////////////初始化硬件/////////////////////////////

    thermocouple = &thermocouple1;
    
    //获取系统信息
    ChipMAC = ESP.getEfuseMac();
    sprintf(CompileTime, "%s %s", __DATE__, __TIME__);
    for (uint8_t i = 0; i < 6; i++)
        sprintf(ChipMAC_S + i * 3, "%02X%s", ((uint8_t*) &ChipMAC)[i], (i != 5) ? ":" : "");

    //初始化串口
    Serial.begin(115200);

    
    

    //初始化GPIO
    BeepInit();                     //蜂鸣器

    pinMode(POWER_ADC_PIN, INPUT);  //主电压分压检测ADC


    //初始化烙铁头
    TipControlInit();

    //初始化编码器
    sys_RotaryInit();

    //初始化OLED
    Disp.begin();
    Disp.setBusClock(921600);
    Disp.enableUTF8Print();
    Disp.setFontDirection(0);
    Disp.setFontPosTop();
    Disp.setFont(u8g2_font_wqy12_t_gb2312);
    Disp.setDrawColor(1);
    Disp.setFontMode(1);

    ////////////////////////////初始化软件/////////////////////////////
    //显示启动信息
    //ShowBootMsg();

    //启动文件系统，并读取存档
    FilesSystemInit();

    //初始化命令解析器
    shellInit();

    //初始化蓝牙（可选）
    BLE_Init();

    SetSound(BootSound); //播放音效

    // Max6675Init();
    


    //初始化UI
    System_UI_Init();

    //首次启动的时候根据启动温度配置，重新设定目标温度
    sys_Counter_SetVal(BootTemp);

    //载入烙铁头配置
    LoadTipConfig();

    //显示Logo
//    EnterLogo();

    //开机密码
    while (!EnterPasswd())
    {
        Pop_Windows("身份验证失败");
    }
    SYS_Ready = true;

}

void loop()
{
    //获取按键
    sys_KeyProcess();

    if (!Menu_System_State)
    {
        //温度闭环控制
        TemperatureControlLoop(thermocouple);
        //更新系统事件：：系统事件可能会改变功率输出
        TimerEventLoop();
        
    }


    //更新状态码
    SYS_StateCode_Update();
    //设置输出功率
    SetPOWER(PID_Output);

    //刷新UI
    System_UI();
}
/**
 * @description: 计算主电源电压
 * @param {*}
 * @return 主电源电压估计值
 */
double Get_MainPowerVoltage(void)
{
    //uint16_t POWER_ADC = analogRead(POWER_ADC_PIN);
    double TipADC_V_R2 = analogReadMilliVolts(POWER_ADC_PIN) / 1000.0;
    //double   TipADC_V_R2 = ESP32_ADC2Vol(POWER_ADC);
    double TipADC_V_R1 = (TipADC_V_R2 * POWER_ADC_VCC_R1) / POWER_ADC_R2_GND;

    SYS_Voltage = TipADC_V_R1 + TipADC_V_R2;
    return SYS_Voltage;
}

void SYS_Reboot(void)
{
    ESP.restart();
}

void About(void)
{
    //播放Logo动画
    EnterLogo();
    //生成项目QRCode
    QRCode qrcode;
    uint8_t qrcodeData[qrcode_getBufferSize(3)];

    switch (Language)
    {
        case LANG_Chinese:
            qrcode_initText(&qrcode, qrcodeData, 3, 0, "https://gitee.com/createskyblue/OpenT12");
            break;

        default:
            qrcode_initText(&qrcode, qrcodeData, 3, 0, "https://github.com/createskyblue/OpenT12");
            break;
    }

    Clear();

    uint8_t x_offset = (SCREEN_COLUMN - qrcode.size * 2) / 2;
    uint8_t y_offset = (SCREEN_ROW - qrcode.size * 2) / 2;

    for (uint8_t y = 0; y < qrcode.size; y++)
        for (uint8_t x = 0; x < qrcode.size; x++)
            if (qrcode_getModule(&qrcode, x, y))
                Draw_Pixel_Resize(x + x_offset, y + y_offset, x_offset, y_offset, 2, 2);

    Disp.setDrawColor(2);
    Disp.drawBox(x_offset - 2, y_offset - 2, qrcode.size * 2 + 4, qrcode.size * 2 + 4);
    Disp.setDrawColor(1);

    while (!sys_KeyProcess())
    {
        Display();
    }

}

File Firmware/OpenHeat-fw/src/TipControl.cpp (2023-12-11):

#include "OpenT12.h"


//[既然有了nmos 为啥还要pmos]科普:https://www.bilibili.com/video/BV1Mb4y1k7fd?from=search&seid=15411923932488650975

enum MOS_Type
{
    PMOS = 0,
    NMOS = 1
};
//PWM
double PWM_Freq = 50000;    // uint8_t类型写错了，改为double类型
                            // 将频率从默认的2000改为50000，开关电源模块电感没有吱吱响声了
                            // 备注：PC817 光耦带宽 81KHz
uint8_t PWM1_Channel = 0;    // 通道
uint8_t PWM2_Channel = 0;    // 通道
uint8_t PWM_Resolution = 8;  // 分辨率
//基础温控
uint8_t MyMOS = NMOS;
uint8_t POWER = 0;
uint8_t PWM = 0;
uint8_t LastPWM = 0;
uint16_t LastADC = 0;
double TipTemperature = 0;
double PID_Output = 0;
double PID_Setpoint = 0;
double *ptr_PID_Setpoint = &PID_Setpoint;
double TempGap = 0;
uint32_t ADCSamplingInterval = 0; //ADC采样间隔(ms)
//PID
float readyKp = 1.0, readyKi = 0, readyKd = 0.05;    //用于避免刚上电热床还没温升阻值过小导致开关电源短路保护的预备PID参数
float aggKp = 7.0, aggKi = 0, aggKd = 0.2;
float consKp = 30.0, consKi = 1, consKd = 0.5;


//初始化烙铁头温控系统
void TipControlInit(void)
{
    //初始化ADC输入GPIO
    pinMode(TIP_ADC_PIN, INPUT_PULLUP); //ADC

    ledcAttachPin(PWM1_PIN, PWM1_Channel);  // 绑定PWM1通道
    ledcSetup(PWM1_Channel, PWM_Freq, PWM_Resolution); // 设置PWM1通道

    if (PWM2_PIN != -1)
    {
        ledcAttachPin(PWM2_PIN, PWM2_Channel);  // 绑定PWM2通道
        ledcSetup(PWM2_Channel, PWM_Freq, PWM_Resolution); // 设置PWM2通道
    }

    SetPOWER(0); //关闭功率管输出

    if (SW_PIN != -1)
    {
        //初始化SW-PIN休眠检测引脚
        pinMode(SW_PIN, INPUT_PULLUP);
        //初始化SW-PIN休眠检测引脚中断 (尽可能减少中断的使用)
        //attachInterrupt(SW_PIN, SW_IRQHandler, CHANGE);
    }

    //初始化烙铁头PID
    MyPID.SetOutputLimits(0, 255); //PID输出限幅
    MyPID.SetMode(AUTOMATIC); //PID控制模式
    MyPID.SetSampleTime(10); //PID采样时间
}

//计算实际温度
double CalculateTemp(double ADC, double P[])
{
    // TipTemperature = P[0] + ADC * P[1] + ADC * ADC * P[2] + ADC * ADC * ADC * P[3];
    return TipTemperature;
}

//PWM输出模块
uint8_t PWMOutput_Lock = true;
void PWMOutput(uint8_t pwm)
{
    PWM_WORKY = true;
    //PWM锁
    if (PWMOutput_Lock || ShutdownEvent || Menu_System_State || ERROREvent)
    {
        PWM_WORKY = false;
        // Log(LOG_INFO,"输出被限制");
        // printf("输出被限制 PWMOutput_Lock=%d ShutdownEvent=%d Menu_System_State=%d ERROREvent=%d\n", PWMOutput_Lock, ShutdownEvent, Menu_System_State, ERROREvent);
        if (MyMOS == PMOS) pwm = 255;
        else pwm = 0;

        // //软件指示灯
        // digitalWrite(LED_Pin ,LOW);
    }
    //printf("PWM:%d\n",pwm);
    if (LastPWM != pwm)
    {
        if (pwm == 255) ledcWrite(PWM1_Channel, 256);
        else ledcWrite(PWM1_Channel, pwm);

        LastPWM = pwm;
    }

}

/**
 *调用卡尔曼滤波器 实践
 */
KFP KFP_Temp = {0.02, 0, 0, 0, 0.01, 4.5};
float SamplingRatioWork = 10;           //采样/加热 比率
//获取ADC读数
int GetADC0(void)
{
    static uint32_t ADCSamplingTime = 0; //上次采样时间
    static uint32_t ADCReadCoolTimer = 0;

    if (SYS_Ready)
    {

        ADCSamplingInterval = millis() - ADCSamplingTime;
        if (ADCSamplingInterval < ADC_PID_Cycle * (9 / 10.0)) return LastADC; //9/10周期ADC不应该工作，应该把时间留给加热

        //若原输出非关闭，则在关闭输出后等待一段时间，因为电热偶和加热丝是串在一起的，只有不加热的时候才能安全访问热偶温度
        if (PWMOutput_Lock == false)
        {
            ADCReadCoolTimer = millis();
            //锁定功率管输出：必须要关闭MOS管才能成功读取电热偶
            PWMOutput_Lock = true;
        }

        if (millis() - ADCReadCoolTimer <= ADC_PID_Cycle / 10)
        {
            return -1; //数据未准备好
        }

    }

    //读取并平滑滤波经过运算放大器放大后的热偶ADC数据
    uint16_t ADC_RAW = analogRead(TIP_ADC_PIN);
    uint16_t ADC;

    //卡尔曼滤波器
    if (Use_KFP) ADC = kalmanFilter(&KFP_Temp, (float) ADC_RAW);
    else ADC = ADC_RAW;
    //printf("%d,%d\r\n", ADC_RAW,ADC);

    //解锁功率管输出：前提是没有打开菜单
    if (!Menu_System_State)
        PWMOutput_Lock = false;

    //记录采样间隔时间
    ADCSamplingTime = millis();

    LastADC = ADC;
    return LastADC;
}

//设置输出功率
void SetPOWER(uint8_t power)
{

    POWER = power;
    //MOS管分类处理
    if (MyMOS == PMOS)
    {
        //PMOS 低电平触发
        PWM = 255 - power;
    }else{
        PWM = power;
    }

    PWMOutput(PWM);
}

float ADC_PID_Cycle_List[3] = {
    1000, // 与目标温度差 大于150度时的PID计算周期
    1000, // 与目标温度差 大于50度小于150度时的PID计算周期
    1000  // 与目标温度差 小于50度时的PID计算周期
};

//温度控制循环
void TemperatureControlLoop(MAX6675 *thermocouple)
{
    Clear();
    // char buffer[50];
    // int ADC;

    PID_Setpoint = sys_Counter_Get();
    if (BoostEvent)
    {
        //短时功率加成
        PID_Setpoint += BoostTemp;
    } else if (SleepEvent)
    {
        PID_Setpoint = SleepTemp;
    }

    PID_Setpoint = constrain(PID_Setpoint, TipMinTemp, TipMaxTemp);
    // //尝试访问ADC
    // ADC = GetADC0();

    static uint32_t ADCSamplingTime = 0; //上次采样时间
    static uint32_t ADCReadCoolTimer = 0;

     if (SYS_Ready)
    {

        ADCSamplingInterval = millis() - ADCSamplingTime;
        if (ADCSamplingInterval < ADC_PID_Cycle * (9 / 10.0)) goto gg; //9/10周期ADC不应该工作，应该把时间留给加热

        // 若原输出非关闭，则在关闭输出后等待一段时间，因为电热偶和加热丝是串在一起的，只有不加热的时候才能安全访问热偶温度
        if (PWMOutput_Lock == false)
        {
            ADCReadCoolTimer = millis();
            //锁定功率管输出：必须要关闭MOS管才能成功读取电热偶
            PWMOutput_Lock = true;
        }

        if(millis() - ADCReadCoolTimer <= ADC_PID_Cycle / 10)
        {
             //数据未准备好
            goto ggg;
        }

         //读取并平滑滤波经过运算放大器放大后的热偶ADC数据
    TipTemperature = thermocouple->readCelsius();

    //解锁功率管输出：前提是没有打开菜单
    if (!Menu_System_State)
        PWMOutput_Lock = false;

    //记录采样间隔时间
    ADCSamplingTime = millis();

    }

    gg: printf("Temp:%lf, ptr_PID_Setpoint:%lf\r\n", TipTemperature, *ptr_PID_Setpoint);
    // if (ADC != -1)
    // TipTemperature = thermocouple->readCelsius();
    if(TipTemperature != 0)
    {

        // TipTemperature = CalculateTemp((double) LastADC, PTemp);
        TempGap = abs(PID_Setpoint - TipTemperature);   //求绝对值

        //根据温差选择合适的ADC-PID采样周期
        if (TempGap > 150) ADC_PID_Cycle = ADC_PID_Cycle_List[0];
        else if (TempGap > 50) ADC_PID_Cycle = ADC_PID_Cycle_List[1];
        else ADC_PID_Cycle = ADC_PID_Cycle_List[2];

        /////////////////////////////////////////////////////////////////////////////////////////////
        //控温模式
        if (PIDMode)
        {
            //PID模式
            
            //根据温度差选择最优的PID配置，PID参数可被Shell实时更改
            if(TipTemperature < ReadyTemp) {
                offset_ReadyTemp = ReadyTemp + 20;
                ptr_PID_Setpoint = &offset_ReadyTemp;
                MyPID.SetTunings(readyKp, readyKi, readyKd);
            }else {
                ptr_PID_Setpoint = &PID_Setpoint;
                if (TempGap < 30) {
                        MyPID.SetTunings(consKp, consKi, consKd);
                    }
                    else {
                        MyPID.SetTunings(aggKp, aggKi, aggKd);
                    }
            }
            //更新PID采样时间：采样时间可被Shell实时更改
            //MyPID.SetSampleTime(PIDSampleTime);
            MyPID.SetSampleTime(ADC_PID_Cycle);
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

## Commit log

2022-02-26 fourth commit
    [125X51-铝壳-前面板.DWG, 125X51-铝壳-后面板.DWG, 125X51-铝壳-壳体.DWG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]
2023-03-25 2023-03-25_最高温度从220改为240度，增加屏幕旋转180度
2023-12-11 2023-12-11_22:02 解决开关电源电感啸叫
